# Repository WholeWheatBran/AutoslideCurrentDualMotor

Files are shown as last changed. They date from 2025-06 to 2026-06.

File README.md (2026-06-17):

**Description**

This project details a module designed to allow two AutoSlide/MultiDrive motors to operate under the parameters of one controller. The module reads the current of the motor circuit to determine both direction and load. This is then used within a PID loop monitoring the current and direction of a second "slave" motor, with its own power supply.

Designed to be used with Cytron MD13S motor driver.

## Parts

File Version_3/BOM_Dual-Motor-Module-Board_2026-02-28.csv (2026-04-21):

ID | Name | Designator | Footprint | Quantity | Manufacturer Part | Manufacturer | Supplier | Supplier Part | Price
1 | P6SMB30CA_C320521 | D1 | SMB_L4.6-W3.6-LS5.3-BI | 1 | P6SMB30CA | LGE(鲁光) | LCSC | C320521 | 0.072
2 | B4B-PH-K-S(LF)(SN) | CN1 | CONN-TH_B4B-PH-K-S | 1 | B4B-PH-K-S(LF)(SN) | JST | LCSC | C131334 | 0.045
3 | JK30-500_C369108 | F2 | FUSE-TH_L14.0-W3.0-P10.20-D1.2-S1.2 | 1 | JK30-500 | JK(金科) | LCSC | C369108 | 0.122
4 | 5.6uH | L1 | IND-SMD_L1.8-W1.3-1 | 1 | YWLD1608-5R6K | YJYCOIN(益嘉源) | LCSC | C5339206 | 0.062
5 | 10uF | C6 | CAP-TH_BD5.0-P2.00-D0.8-FD | 1 | 50YXJ10M5X11 | Rubycon(红宝石) | LCSC | C432355 | 0.051
6 | ARDUINO_NANO | U1 | COMM-TH_ARDUINO_NANO | 1 | ARDUINO_NANO | null | LCSC | C9900017879
7 | 1nF | C1,C2 | C0603 | 2 | CC0603KRX7R9BB102 | YAGEO(国巨) | LCSC | C100040 | 0.002
8 | 10kΩ | PD_POT | RES-ADJ-TH_3362P | 1 | 3362P-1-103 | BOCHEN(博晨) | LCSC | C118956 | 0.148
9 | 10kΩ | R1,R2 | R0402 | 2 | 0402WGF1002TCE | UNI-ROYAL(厚声) | LCSC | C25744 | 0.001
10 | 100nF | C3,C4,C5 | C0603 | 3 | CC0603KRX7R9BB104 | YAGEO(国巨) | LCSC | C14663 | 0.002
11 | 10uF | C7,C8 | C0805 | 2 | GRM21BR61H106KE43L | muRata(村田) | LCSC | C440198 | 0.067
12 | 1kΩ | R3,R4,R5 | R0603 | 3 | 0603WAF1001T5E | UNI-ROYAL(厚声) | LCSC | C21190 | 0.001
13 | S6B-PH-K-S-(LF)(SN) | MM_IN,MM_OUT,SM_IN | CONN-TH_6P-P2.00_S6B-PH-K-S-LF-SN | 3 | S6B-PH-K-S(LF)(SN) | JST | LCSC | C157920 | 0.061
14 | S2B-PH-K-S(LF)(SN) | SM_OUT,SP_IN,SP_OUT | CONN-TH_S2B-PH-K-S-LF-SN | 3 | S2B-PH-K-S(LF)(SN) | JST | LCSC | C173752 | 0.038
15 | ACS712ELCTR-05B-T | MM_SENSOR,SM_SENSOR | SOIC-8_L5.0-W4.0-P1.27-LS6.0-BL | 2 | ACS712ELCTR-05B-T | ALLEGRO(美国埃戈罗) | LCSC | C44471 | 1.083
16 | TSR 1-2450_C6886877 | 24V-5V | PWRM-TH_L11.7-W7.5_TSR1-2450 | 1 | TSR 1-2450 | TRACO POWER | LCSC | C6886877 | 5.587

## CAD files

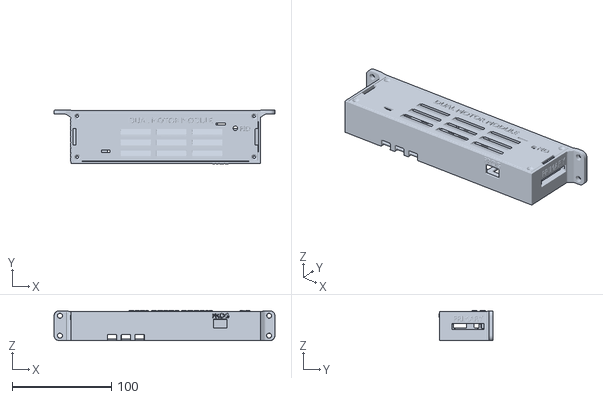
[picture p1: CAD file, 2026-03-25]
Version_3/DMMPCB_Case_V0.3.stl
222.3 x 53.9 x 30.5

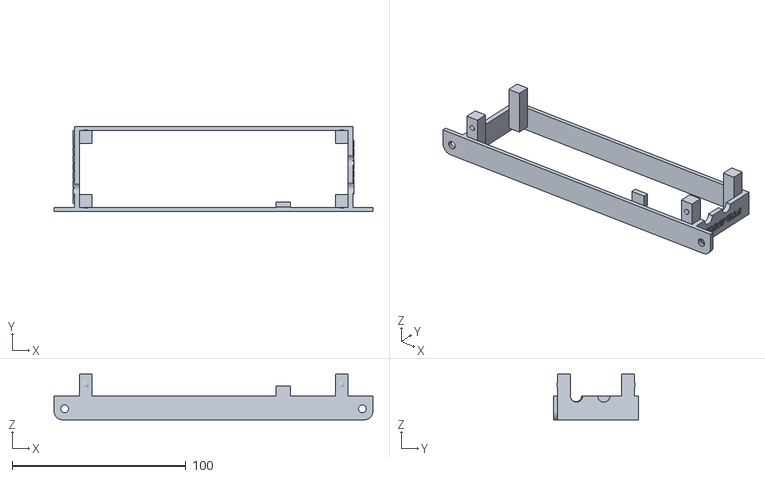
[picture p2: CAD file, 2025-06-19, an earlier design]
Version_1/MID.stl
183.8 x 48.8 x 26.4

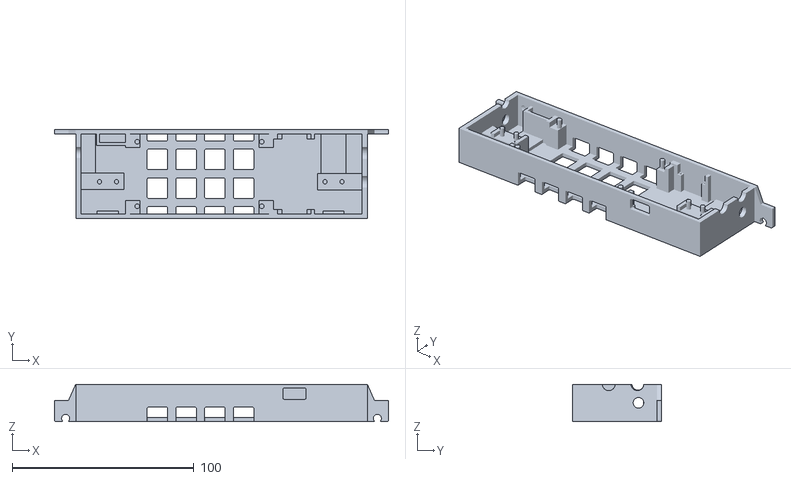
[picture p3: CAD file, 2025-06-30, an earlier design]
Version_2/CURRENT MODULE V3 BASE.stl
183.8 x 48.8 x 20.6

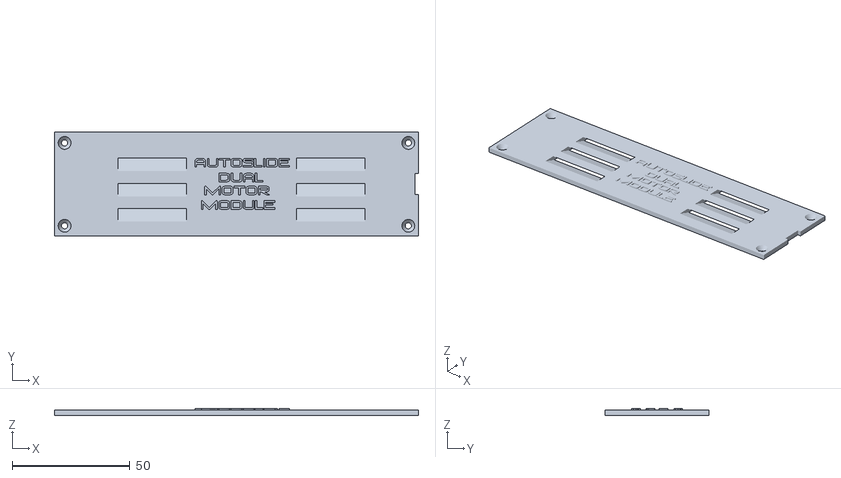
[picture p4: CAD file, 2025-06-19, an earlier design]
Version_1/COVER.stl
154.5 x 44.0 x 2.91

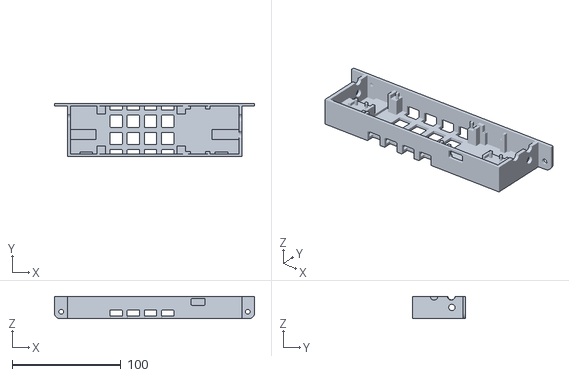
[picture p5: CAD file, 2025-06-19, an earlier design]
Version_1/BASE.stl
183.8 x 48.8 x 20.5

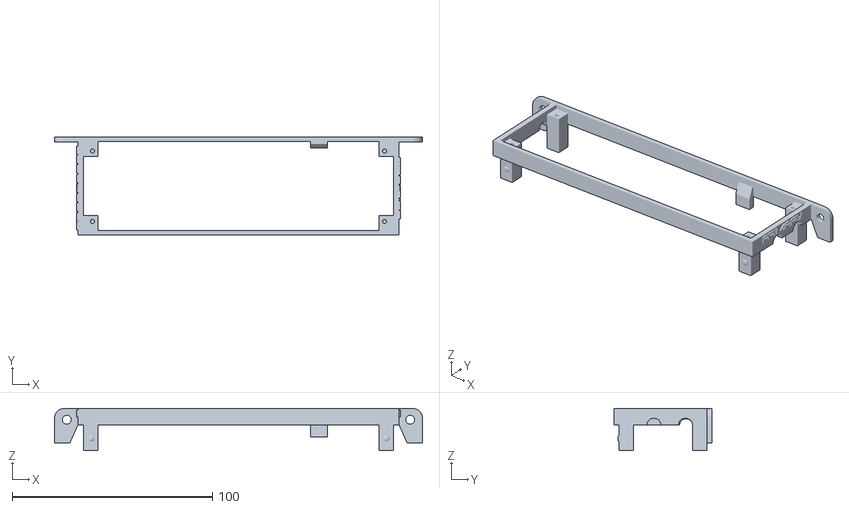
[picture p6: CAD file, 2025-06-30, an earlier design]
Version_2/CURRENT MODULE V3 MID.stl
183.8 x 48.8 x 21.1

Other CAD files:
Version_2/CURRENT MODULE V3 COVER.stl
Version_1/CURRENT MODULE V2.blend

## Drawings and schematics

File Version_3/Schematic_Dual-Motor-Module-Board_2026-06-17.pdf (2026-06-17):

## ARDUINO NANO CONTROLLER PINOUT

# DUAL MOTOR MODULE

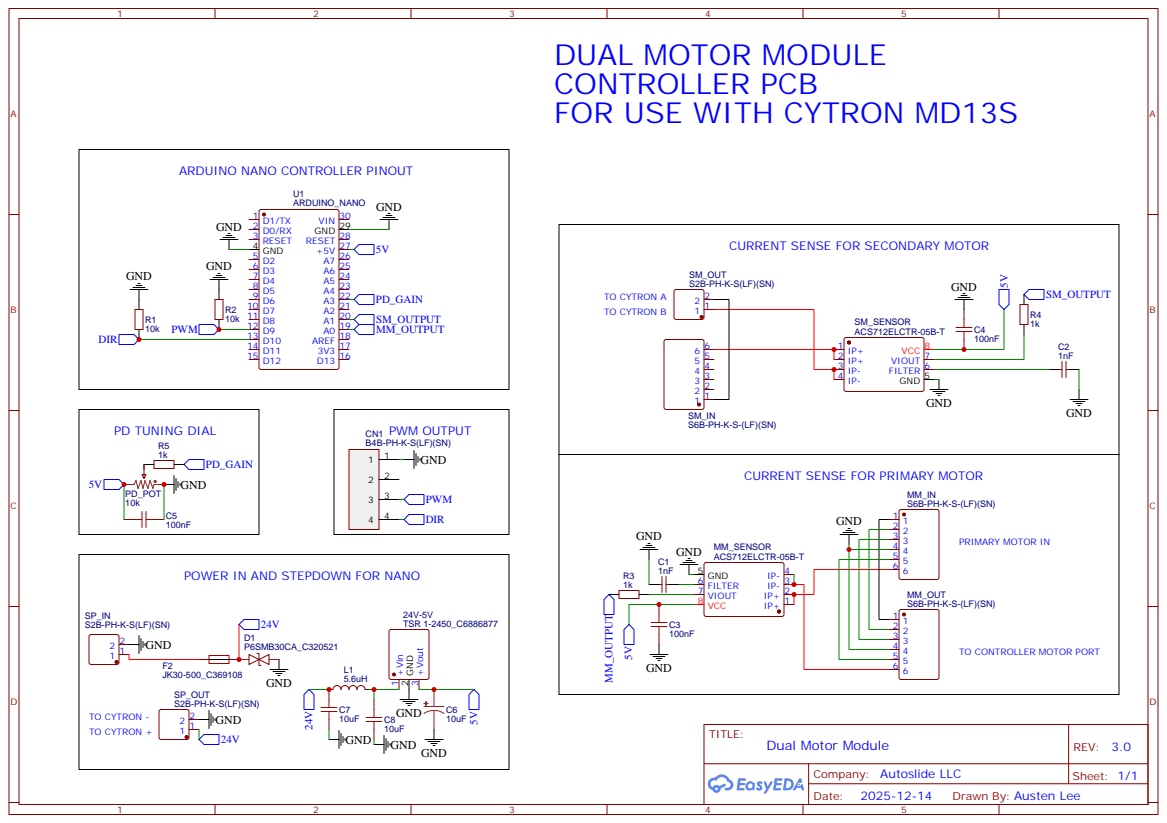
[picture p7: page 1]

CONTROLLER PCB
FOR USE WITH CYTRON MD13S

CURRENT SENSE FOR SECONDARY MOTOR

CURRENT SENSE FOR PRIMARY MOTOR

POWER IN AND STEPDOWN FOR NANO

TO CONTROLLER MOTOR PORT

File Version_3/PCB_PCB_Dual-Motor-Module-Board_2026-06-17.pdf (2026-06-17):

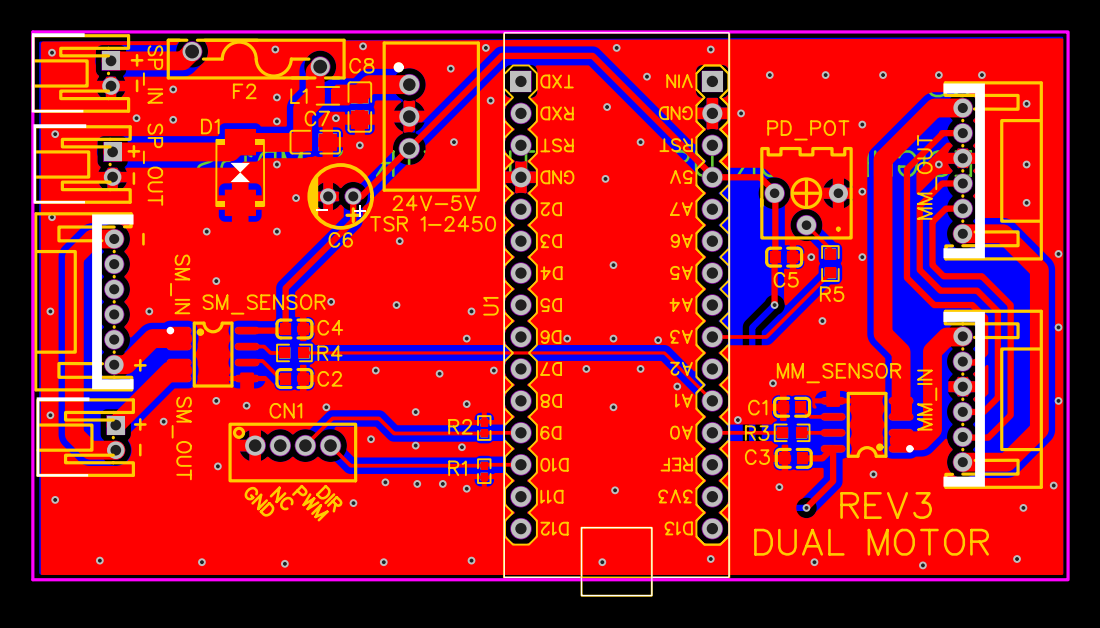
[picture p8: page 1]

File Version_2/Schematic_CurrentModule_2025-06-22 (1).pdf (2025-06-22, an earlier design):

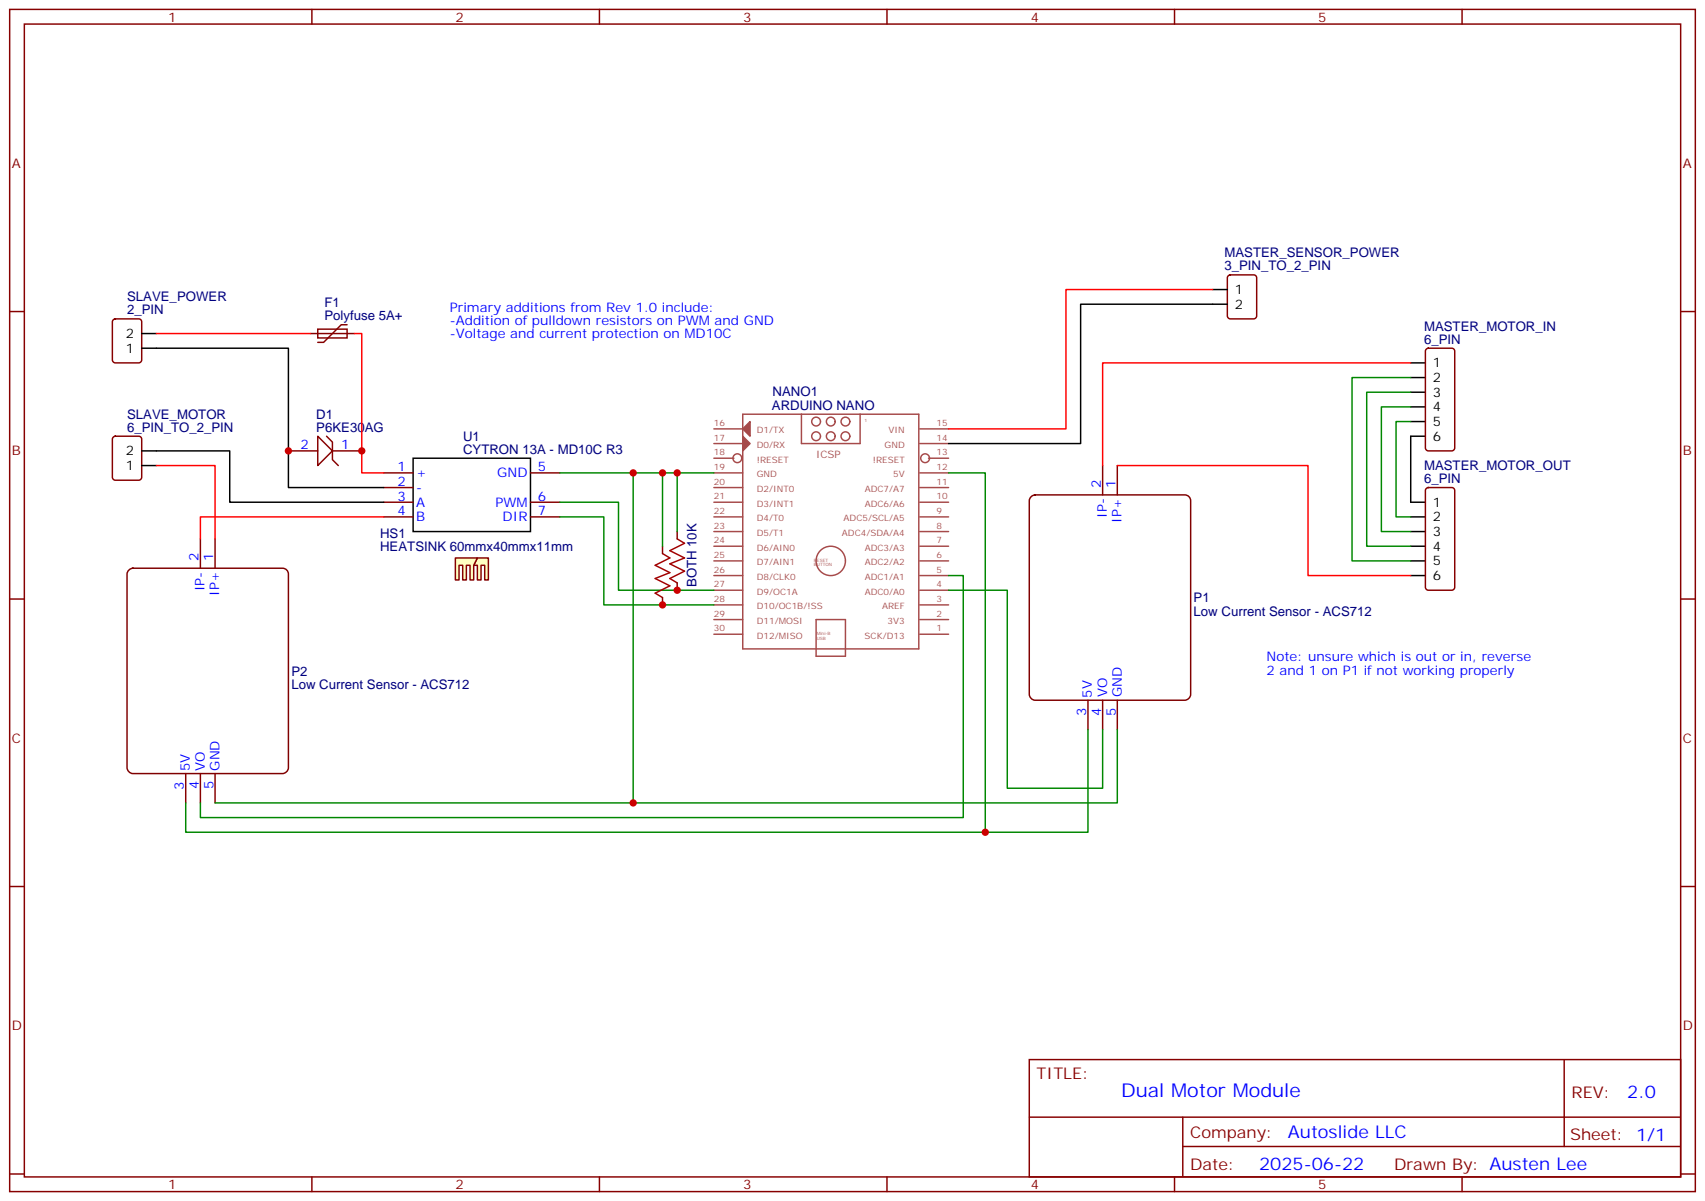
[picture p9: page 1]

Primary additions from Rev 1.0 include:
-Addition of pulldown resistors on PWM and GND
-Voltage and current protection on MD10C

Note: unsure which is out or in, reverse
2 and 1 on P1 if not working properly

Drawn By: Austen Lee

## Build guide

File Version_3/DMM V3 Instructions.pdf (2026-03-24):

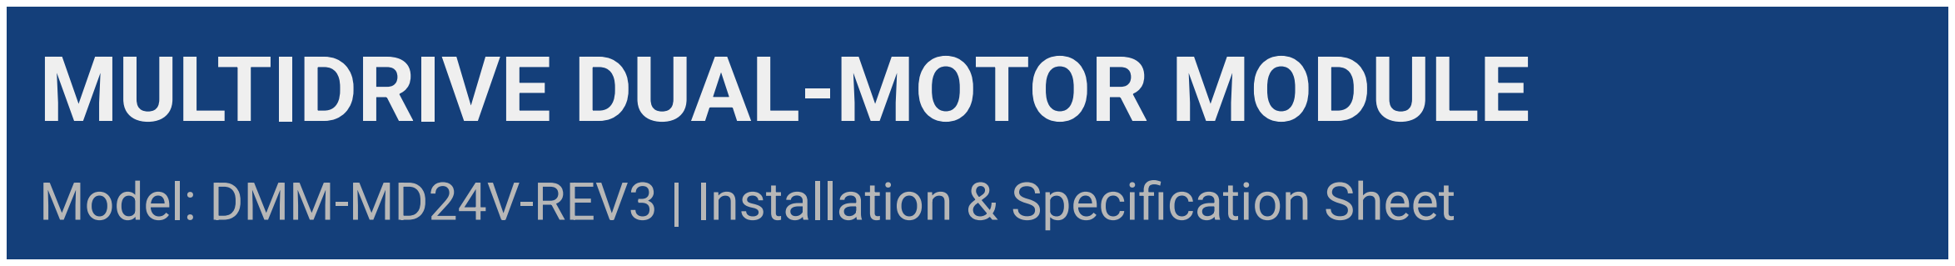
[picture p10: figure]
MULTIDRIVE DUAL-MOTOR MODULE

## Model: DMM-MD24V-REV3 | Installation & Specification Sheet

## Product Overview

The DMM-MD24V-REV3 (Dual Motor Module) is a control module designed for the Autoslide MultiDrive automatic sliding door system, employing a dual-motor configuration on large sliding doors requiring heavy opening and closing force. This unit ensures smooth, synchronized operation by actively monitoring the current draw of the primary motor and adjusting the secondary motor in real-time. The module is compliant with the existing sliding rail component system in the MultiDrive, and should be slid directly adjacent to the main controller and motor.

## Technical Specifications

Compatible Motor Type | Autoslide LLC MultiDrive 24VDC Brushed Motor
Power Supply Input | 24VDC, 2.7A (Regulated)
Secondary Motor Driver | Cytron MD13S (Integrated)
Control Methodology | Active PID Current Equalization Loop (adjustable via dial)
Circuit Protection | Polyfuse (Overcurrent), TVS Diode (Transient Voltage Suppression)
Mounting Interface | Standard railing system slide-mount

## Interface & Port Layout

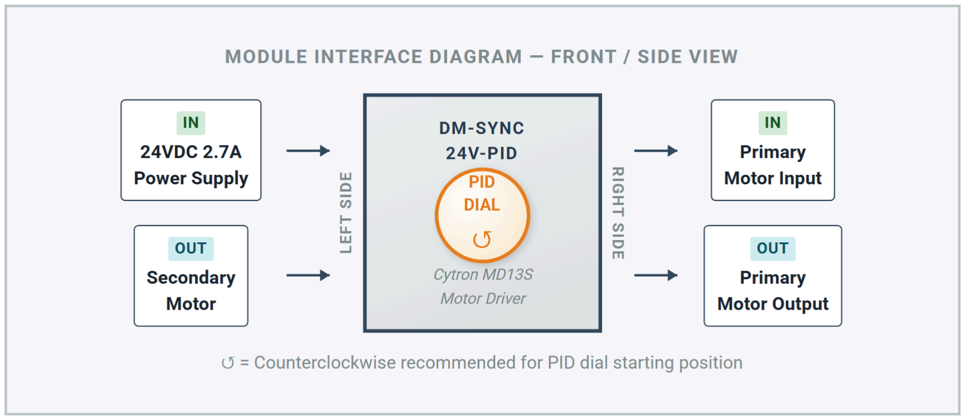
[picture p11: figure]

© 2026 Autoslide LLC. All rights reserved. Specifications subject to change without notice.

## Installation Instructions

## Necessary Parts

- 1x Dual Motor Module
- 1x MultiDrive Motor (to be used as secondary motor)
- 1x MultiDrive Power Supply (to be used as secondary power supply)
- MultiDrive Motor Extension Cabling
- 1x Complete MultiDrive Kit (includes primary motor, controller, primary power supply)

## Part 1 - Physical Setup

1. Pre-Assembly: Prior to mounting, pre-assemble the MultiDrive system per its standard instructions. In place of a belt tensioner on one side of the door, install the secondary motor and secondary power supply. Both power supplies should be located near the MultiDrive controller. Position the Dual Motor Module immediately next to the controller and primary motor for optimal cable routing.
2. Motor Mounting: Tighten one motor securely in place, and leave the other motor very slightly loose so it can be adjusted during belt tensioning.
3. Belt Routing: After mounting the system onto the door, feed the MultiDrive belt through both motors. Pull the belt tightly (while ensuring both motors remain in place), then cut and connect the belt ends per the standard MultiDrive instructions.
4. Belt Tensioning: Using a prying tool or ratchet strap, manually pull the loose motor as far from the fixed motor as possible to tension the belt. If necessary, have a helper support the middle of the belt to minimize slack. The belt should be as tight as possible to prevent slipping before tightening the second motor fully in place.

## Part 2 - Cable and Module Setup

1. Primary Motor IN (Right Side): Plug the cable coming from the primary motor — the motor closest to the MultiDrive Controller — into the open Primary Motor IN port on the right side of the Dual Motor Module.
2. Primary Motor OUT to Controller (Right Side): Plug the motor cable coming out of the Primary Motor OUT port on the right side of the Dual Motor Module into the Motor port on the MultiDrive Controller.
3. Secondary Motor (Left Side): Plug the secondary motor — the motor furthest from the MultiDrive Controller — into the open Secondary Motor OUT port on the left side of the Dual Motor Module.
4. Secondary Power Supply (Left Side): Plug the 24VDC 2.7A secondary power supply into the open Power Supply IN port on the left side of the Dual Motor Module. Verify polarity before connecting.
5. Power On & Programming: Once all connections are complete, proceed with powering on and programming the MultiDrive system as normal.

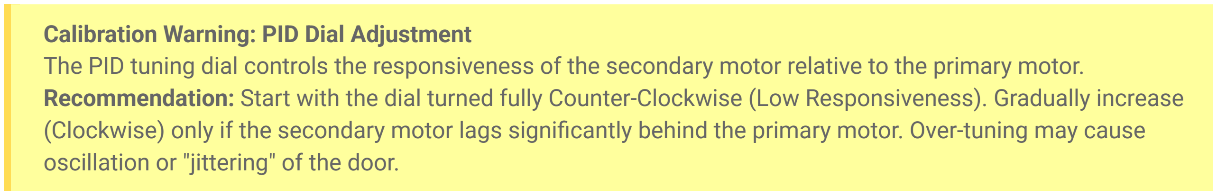
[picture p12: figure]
oscillation or "jittering" of the door.

Calibration Warning: PID Dial Adjustment
The PID tuning dial controls the responsiveness of the secondary motor relative to the primary motor. Recommendation: Start with the dial turned fully Counter-Clockwise (Low Responsiveness). Gradually increase (Clockwise) only if the secondary motor lags significantly behind the primary motor. Over-tuning may cause

© 2026 Autoslide LLC. All rights reserved. Specifications subject to change without notice.

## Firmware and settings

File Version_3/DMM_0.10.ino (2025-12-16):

/*
   AUTOSLIDE DUAL MOTOR MODULE
   Designed by Austen Brandon Lee, 2025
   Meant for replicating current using ATM3.9B from one motor to another motor.

   Circuit Diagram Overview
   ========================
  
  ---------------------------

  Update Log:
  - 06/13/25: V0.01 - Adapted from old voltage emulator module. Monitors current and distributes load between two motors
  - 11/07/25: V0.05 - Tweaked PID to decrease oscillations in belt caused by master-slave current difference. Increased d and slightly increased filtering.
  - 11/11/25: V0.06 - Added PD_Alpha to linearly adjust P and D for different load. Future improvement can be adjusting this with physical dial.
  - 11/20/25: V0.07 - Added analog dial to A3 to allow manual tuning of PD_ALPHA without needing to reflash.
  - 12/16/25: V0.10 - Set minimum PWM to 0 to prevent backwards runaway PWM. Tested with prototype PCBs.
*/

#define VERSION_NUMBER 0.1

#include <avr/wdt.h>
#include <Wire.h>

// SETTINGS

#define MASTER_SLAVE_SHARING 50         // PERCENT. Percentage of total load taken by master. 50 means 50% (equally shared). DO NOT SET TO 0. Smaller values mean slave does more.

#define RAW_CURRENT_DEADZONE 50         // mA. Zero out current readings below this level.
#define CURRENT_FILTERING_ALPHA 0.05    // Smoothing factor (0 = heavy smoothing, 1 = no smoothing)
#define FILTERED_CURRENT_DEADZONE 20    // mA. Zero out filtered current readings below this level.

#define MAX_CURRENT_MA 5000             // mA. The max current magnitude in the master motor. May be constrained by the INA219 somewhat
#define MIN_EFFECTIVE_PWM 0            // The minimum PWM given to the slave motor during movement

// PID Gains (These are crucial and will need tuning!)
// Start with Ki=0, Kd=0. Tune Kp first. Increase Kp until response is good but not oscillating.
// Then increase Ki slowly to eliminate steady-state error. Then increase Kd slowly to dampen oscillations.
float PD_ALPHA = 1.0;		  			 // Linear adjustment for P and D based on variable load tests - set lower for lower drag (e.g. 0.5)
float Kp_current = 0.35;      // Proportional Gain
#define Ki_current 0.001      			 // Integral Gain
float Kd_current = 0.0155;    // Derivative Gain (start at 0, add if needed for stability)

// SETTINGS

// PINS
#define PWM 9     // PWM output
#define DIR 10    // DIR output
#define MASTER_CURRENT_PIN A0
#define SLAVE_CURRENT_PIN A1
#define DIAL A3
// PINS

// ACS712 SETUPS
#define ACS_ZERO 516            // ACS712 zero-current raw ADC value (adjust based on calibration)
#define ACS_SENSITIVITY 0.185   // V/A for ACS712-5A version (adjust if using 20A or 30A)
#define ADC_TO_VOLT 5.0 / 1023.0
// ACS712 SETUPS

// Filtered values
float filtered_Master_Current = 0.0;
float filtered_Slave_Current = 0.0;
// Filtered values

// Status variables
bool isMoving = false;
bool currentDirection = true;

// PID Controller state variables
float integral_sum = 0.0;
float previous_current_error = 0.0;
unsigned long last_loop_time_ms = 0;  // To calculate DeltaTime for PID
float MAX_INTEGRAL_SUM = 500.0; // Anti-windup for integral term (prevents integral_sum from growing too large)
float previous_d_term = 0;
float d_term_alpha = 0.175;


void setup() {
	pinMode(PWM, OUTPUT);
	pinMode(DIR, OUTPUT);

  // Set Timer1 (pins 9 & 10) to ~31.4 kHz PWM by using no prescaling (prescaler = 1); this is to avoid whine noise
  TCCR1B = TCCR1B & 0b11111000 | 0x01;
  
	Serial.begin(9600);
  Wire.begin();
  Serial.print("Autoslide Dual Motor Driver Version "); Serial.println(VERSION_NUMBER);

  delay(100); // To give time for everything to settle

  last_loop_time_ms = millis();
  wdt_enable(WDTO_2S); // Start watchdog, dat dog, dat diggity dog
}

bool wasMoving, oldDirection; // Just used for output debugging
float current_pwm = 0.0; // Tracks last applied PWM
unsigned long lastPrintTime = 0; // Output debugging only

void loop() {
  wdt_reset(); // Reset watchdog

  // For use in PID loop
  unsigned long current_time_ms = millis();
  float delta_time_sec = (current_time_ms - last_loop_time_ms) / 1000.0; // Convert ms to seconds
  delta_time_sec = constrain(delta_time_sec, 0.001, 0.1); // Clamp to avoid large values if stalled
  last_loop_time_ms = current_time_ms;
  PD_ALPHA = (0.95 * PD_ALPHA) + (0.05 * ((analogRead(DIAL) * 1.15 / 1024.0) + 0.05));
  //Serial.println(PD_ALPHA);

  // Get current readings
  float raw_Master_Current = readCurrent(MASTER_CURRENT_PIN);
  raw_Master_Current = ( (abs(raw_Master_Current) < RAW_CURRENT_DEADZONE) ? 0 : raw_Master_Current);
  filtered_Master_Current = CURRENT_FILTERING_ALPHA * raw_Master_Current + (1 - CURRENT_FILTERING_ALPHA) * filtered_Master_Current;
  filtered_Master_Current = ( (abs(filtered_Master_Current) < FILTERED_CURRENT_DEADZONE) ? 0 : filtered_Master_Current);

  float raw_Slave_Current = readCurrent(SLAVE_CURRENT_PIN);
  raw_Slave_Current = ( (abs(raw_Slave_Current) < RAW_CURRENT_DEADZONE) ? 0 : raw_Slave_Current);
  filtered_Slave_Current = CURRENT_FILTERING_ALPHA * raw_Slave_Current + (1 - CURRENT_FILTERING_ALPHA) * filtered_Slave_Current;
  filtered_Slave_Current = ( (abs(filtered_Slave_Current) < FILTERED_CURRENT_DEADZONE) ? 0 : filtered_Slave_Current);

  // Update status variables
  isMoving = abs(filtered_Master_Current) > 0; // False means not moving, true means moving
  if (isMoving) currentDirection = filtered_Master_Current > 0;

  // Output status updates
  if (isMoving != wasMoving || currentDirection != oldDirection) {
    if (isMoving) {
      Serial.print("Motor is moving "); Serial.println(currentDirection ? "forward." : "backward.");
    } else {
      Serial.println("Motor stopped moving.");
    }
    if (currentDirection != oldDirection && isMoving) {
      analogWrite(PWM, 0);     // Briefly stop PWM
      delay(5);  // Allow DIR pin to settle
    }
    wasMoving = isMoving;
    oldDirection = currentDirection;
  }

  // --- STOP / PID RESET LOGIC ---
  // This critical block runs if the master motor is considered stopped.
  if (!isMoving) {
      analogWrite(PWM, 0); // Stop slave motor
      digitalWrite(DIR, LOW); // Set DIR to a default safe state (e.g., LOW)

      // Reset PID state to prevent integral windup or "jump" when motor restarts. This ensures a smooth start from zero for the slave.
      integral_sum = 0.0;
      previous_current_error = 0.0;
      previous_d_term = 0.0;
      current_pwm = 0;
      last_loop_time_ms = millis(); // Reset time for next calculation (prevents large delta_time_sec)
      return; // Exit loop early; no further calculations needed if not moving
  }

  // Calculate PID error
  // If master takes X%, slave takes (100-X)% of total load. So we want the slave's current to match that ratio.
  float target_Slave_Current = filtered_Master_Current * ( (100.0-MASTER_SLAVE_SHARING) / MASTER_SLAVE_SHARING );
  float current_error = target_Slave_Current - filtered_Slave_Current;

  // Proportional Term
  float p_term = Kp_current*PD_ALPHA * current_error;

  // Integral Term (with anti-windup)
  integral_sum = integral_sum + current_error * delta_time_sec;
  integral_sum = constrain(integral_sum, -MAX_INTEGRAL_SUM, MAX_INTEGRAL_SUM); // Anti-windup
  float i_term = Ki_current * integral_sum;

  // Derivative Term
  float raw_d_term = Kd_current*PD_ALPHA * (current_error - previous_current_error) / delta_time_sec;
  previous_d_term = previous_d_term * (1 - d_term_alpha) + raw_d_term * d_term_alpha;
  float d_term = previous_d_term;
  previous_current_error = current_error;

  // Calculate PID output (this is a change in PWM duty cycle)
  float current_delta = p_term + i_term + d_term; // in mA, this is the difference needed. Can be positive or negative
  
  // Convert to PWM
  float clamped_delta = constrain(current_delta, -MAX_CURRENT_MA, MAX_CURRENT_MA);
  float pwm_delta = (clamped_delta / MAX_CURRENT_MA) * 255.0f;

  current_pwm += pwm_delta; // Apply the delta
  current_pwm = constrain(current_pwm, -255, 255);
  
  // Enforce minimum effective PWM (in either direction)
  if (current_pwm > 0 && current_pwm < MIN_EFFECTIVE_PWM) {
    current_pwm = MIN_EFFECTIVE_PWM;
  } else if (current_pwm < 0 && current_pwm > -MIN_EFFECTIVE_PWM) {
    current_pwm = -MIN_EFFECTIVE_PWM;
  }

  // Set DIR based on sign of PWM
  digitalWrite(DIR, current_pwm >= 0 ? LOW : HIGH);

  // Write the absolute PWM value
  analogWrite(PWM, (int)abs(current_pwm));

  // OUTPUT DEBUGGING SECTION
  if (current_time_ms - lastPrintTime >= 500) {
    Serial.print("Master current: "); Serial.println(filtered_Master_Current);
    Serial.print("Slave current: "); Serial.println(filtered_Slave_Current);
    Serial.print("Current difference: "); Serial.println(filtered_Slave_Current - filtered_Master_Current);
    Serial.print("Slave PWM output: "); Serial.println(current_pwm);
    Serial.print("Slave DIR output: "); Serial.println(current_pwm >= 0 ? "LOW" : "HIGH");

    lastPrintTime = current_time_ms;
  }
  
}

// Reads ACS712 sensor and returns current in mA
float readCurrent(int pin) {
  int raw = analogRead(pin);
  float voltage = raw * ADC_TO_VOLT;
  float deltaV = voltage - (ACS_ZERO * ADC_TO_VOLT);
  float currentA = deltaV / ACS_SENSITIVITY;
  return currentA * 1000.0;
}

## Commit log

2025-06-17 Delete CurrentModuleSetup.blend
    Old version
2025-06-19 Add files via upload
    Updated printable casing, including higher roof to accommodate Dupont connectors and bigger holes for motor cables
    [BASE.stl, COVER.stl, CURRENT MODULE V2.blend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]
2025-06-22 Circuit diagram for assembly
2025-06-30 Add files via upload
    Updated STL files for housing
    [CURRENT MODULE V3 BASE.stl, CURRENT MODULE V3 COVER.stl, CURRENT MODULE V3 MID.stl]
2025-11-07 Add Dual Motor Firmware V0.05 implementation
    This file contains the implementation of the Autoslide Dual Motor Module, including PID control for motor current distribution and settings for motor operation.
2025-11-11 Increment version to 0.06 and adjust PID gains
    Updated version number to 0.06 and modified PID gains to include PD_ALPHA for load adjustment.
2025-12-16 Add DMM_0.10.ino for dual motor control
    New firmware for use on REV2 PCBs.
2026-03-13 Casing STL
    Version 0.3 of casing for dual motor module, using Rev2 PCB and Cytron MD13S. Casing has been adjusted for usage with slide rails from AutoSlide controller module.
    [DMMPCB_Case_V0.3.stl]
2026-03-25 Updated casing files with fixed board placement
    updated board clips to prevent movement
    [DMMPCB_Case_V0.3.stl]
2026-06-17 Add files via upload
    Addition of circuit diagram and layout diagram of PCB
2026-06-17 Clean up file directory before review
    [BOM_Dual-Motor-Module-Board_2026-02-28.csv, DMMPCB_Case_V0.3.stl, PickAndPlace_PCB_Dual-Motor-Module-Board_2026-02-28.csv]
